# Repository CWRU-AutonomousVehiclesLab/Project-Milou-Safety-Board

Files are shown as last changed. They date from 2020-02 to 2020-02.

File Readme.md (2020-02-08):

# Project Milou Safety Board
This repo contains Project Milou's safety board design. The goal of this design is to have a standardized modular designed board that allow other competitor to improve their safety system.





## What is Project Milou?
Project Milou is Case Western Reserve University's second autonomous snowplow robot. The robot actively participate in the ION Autonomous Snowplow Challenge. Currently the latest revision of the robot is utilizing a Teensy 3.6, an ITX computer with a core i5 as its main control system.

## Logistics

**Latest revision is done at Febuary, 2020.**

The designer of this board can be traced back maybe 5 years, designed by folks working with Project Otto. This board re-layed out by Ziyi Huang as part of fullfilment for his senior project fall 2019. The board is modified by Frank (Chude Qian) to make it work on the robot. 

This project is maintained under CWRU Auontomous Vehicles Lab till 2021, and further maintained under CWRU Biologically Inspired Robotics (Biorobotics) Center. 

*Copyright belongs to CWRU Autonomous Vehicles lab, CWRU Biologically Inspired Robotics (Biorobotic) Center. Please use with acknowledgement.*

### Contact for questions
To contact email [Frank](mailto:cxq41@case.edu) if it is before 2021. If it is after 2021, email [Ian](mailto:ija2@case.edu) and [Dr. Merat](mailto:flm@case.edu). 

## How to use this?
To use the safety board design, you do not necessarily need to know about making PCBS. We recommend you to have some basic understanding of Egale the PCB software if you want to modify it. It should be fairly easy to use on a standardized ROS enabled robot.

### Pressumptions
The board assumes the following components: a 5V supply, a 12V supply, a standard RC Spread Specturum 2.4G remote reciever, a digital microcontroller that is capable of 5V or 3.3V digital input and output, a standard E-stop Button and a 12V relay.

### Materials
In order to use this PCB board, you will have to manufature it. We recommend [JLCPCB](https://jlcpcb.com/) which only cost about 10 USD for 5 boards. Unless you are mass manufacturing it, for sampling purposes, it should be good enough.

### Putting it together
In BOM folder, you will be able to find an excel sheet where it includes all of the materials you will need to put the board together. **NOTE: Do not use the value on the Eagle Schematics as they might by faulty. It is only used for manufacturing the PCB purpose.**

### 5V or 3.3V?
This board supports both 5V logic system and 3.3V logic system. If you need to have the logic output of the board to a 5V system, you should not solder R19 and R17 (aka a voltage divider to step down the 5V logic).

If your input voltage is normally 5V, I would recommend you use the Q4 component for Q5, instead of listed.

### Wiring it up!
Once you have completed all the steps above, you should be able to wire it up. To do so, start from left to right. The left side are all of the inputs.

**Supply**: The top of the supply terminal is +5V logic voltage, it is also used to power your Remote Reciever. A Ground is then followed. A 12V rail for driving the relay, and another ground.

**RCV-CH3**: For this 4 pin terminal, the top pin is your actual signal, and the middle one is 5V, and the bottom one is GND. Note that the last pin is not used, and additionally, the 5V pin can be disconnected if your RC reciever runs on a different voltage system. However, make sure that your GND is connected so that the system runs on the same reference.

**TEENSYIN** For this terminal, the top two are responsible for tracking the microcontroller output. This is designed allowing the microcontroller to throw an Estop exception and allowing the robot to be safely disabled from software. If your design do not have this feature, simply follow the 5V logic guideline and apply 5V directly on to the terminal. The bottom two are responsible for the Red ESTOP button. Simply wire the button to those two leads.

**TEENSYOUT** This is 4pin terminal on the right. This is all the output terminals. The top 2 terminals are wired directly to a relay to further drive a contactor for the robot. These two pin will run on 12V so make sure not to get it onto your microcontroller. The bottom two are signal for the microcontroller, allowing it to read the state of the ESTOP board. As always, top is signal, and bottom is GND. 

The board is designed to provide you ground wherever you might needed. For best practice you can also use twisted cable for delivering signal and reduce circuit noise interference.

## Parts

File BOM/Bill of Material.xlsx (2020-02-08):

Part | Value | Device | Package | Description | Multi Voltage OP Note
RCV_CH3 | 1X4-CLEANBIG | 1X4-CLEANBIG | 1X04-CLEANBIG | 4-pin connector
SUPPLY | 1X4-CLEANBIG | 1X4-CLEANBIG | 1X04-CLEANBIG | 4-pin connector
TEENSYIN | 1X4-CLEANBIG | 1X4-CLEANBIG | 1X04-CLEANBIG | 4-pin connector
TEENSYOUT | 1X4-CLEANBIG | 1X4-CLEANBIG | 1X04-CLEANBIG | 4-pin connector
C3 | .1uF | C10/4 | C10B4 | CAPACITOR
C4 | .1uF | C10/4 | C10B4 | CAPACITOR
C1 | .01uF | C5/2.5 | C5B2.5 | CAPACITOR
C2 | .01uF | C5/2.5 | C5B2.5 | CAPACITOR
C5 | .01uF | C5/2.5 | C5B2.5 | CAPACITOR
C6 | .01uF | C5/2.5 | C5B2.5 | CAPACITOR
C7 | .01uF | C5/2.5 | C5B2.5 | CAPACITOR
C8 | .01uF | C5/2.5 | C5B2.5 | CAPACITOR
U3 | SN74HC08N | SN74HC08N | DIP254P762X508-14 | QUADRUPLE 2-INPUT POSITIVE-NOR GATES
U4 | SN74HC74N | SN74HC74N | DIP254P762X508-14 | DUAL D-TYPE POSITIVE-EDGE-TRIGGERED FLIP-FLOPS
U1 | NE555 | NE555 | DIP794W45P254L1060H508Q8 | 555 timer
U2 | NE555 | NE555 | DIP794W45P254L1060H508Q8 | 555 timer
D3 | 1N4446 | 1N4446 | DO35-10 | DIODE
D1 | 1N4004 | 1N4004 | DO41-10 | DIODE
R1 | 10K | RHPS58 | HPS58 | Power Resitor
R10 | 10K | RHPS58 | HPS58 | Power Resitor
R11 | 10K | RHPS58 | HPS58 | Power Resitor
R12 | 1K | RHPS58 | HPS58 | Power Resitor
R13 | 1K | RHPS58 | HPS58 | Power Resitor
R14 | 1K | RHPS58 | HPS58 | Power Resitor
R15 | 33K | RHPS58 | HPS58 | Power Resitor
R16 | 33K | RHPS58 | HPS58 | Power Resitor
R17 | 33k | RHPS58 | HPS58 | Power Resitor | Optional, not needed for 5v output
R18 | 5.6K | RHPS58 | HPS58 | Power Resitor
R19 | 56k | RHPS58 | HPS58 | Power Resitor | Optional, not needed for 5v output
R2 | 10K | RHPS58 | HPS58 | Power Resitor
R3 | 10K | RHPS58 | HPS58 | Power Resitor
R4 | 10K | RHPS58 | HPS58 | Power Resitor
R5 | 10K | RHPS58 | HPS58 | Power Resitor
R6 | 10K | RHPS58 | HPS58 | Power Resitor
R7 | 15K | RHPS58 | HPS58 | Power Resitor
R8 | 200K | RHPS58 | HPS58 | Power Resitor
R9 | 10K | RHPS58 | HPS58 | Power Resitor
LED1 | RED | LED3MM | LED3MM | LED
Q4 | IRF530 | MOSFET-NGDS_TO220V | TO220V | N-Channel Mosfet
Q5 | IRLZ44N | MOSFET-NGDS_TO220V | TO220V | N-Channel Mosfet | Exchangable for 5V operation
Q3 | 2N4403 | 2N4403 | TO92-EBC-OVAL | PNP TRANSISTOR
T1 | 2N4401 | 2N4401 | TO92-EBC-OVAL | NPN TRANSISTOR
T2 | 2N4401 | 2N4401 | TO92-EBC-OVAL | NPN TRANSISTOR
T3 | 2N4401 | 2N4401 | TO92-EBC-OVAL | NPN TRANSISTOR
T4 | 2N4401 | 2N4401 | TO92-EBC-OVAL | NPN TRANSISTOR

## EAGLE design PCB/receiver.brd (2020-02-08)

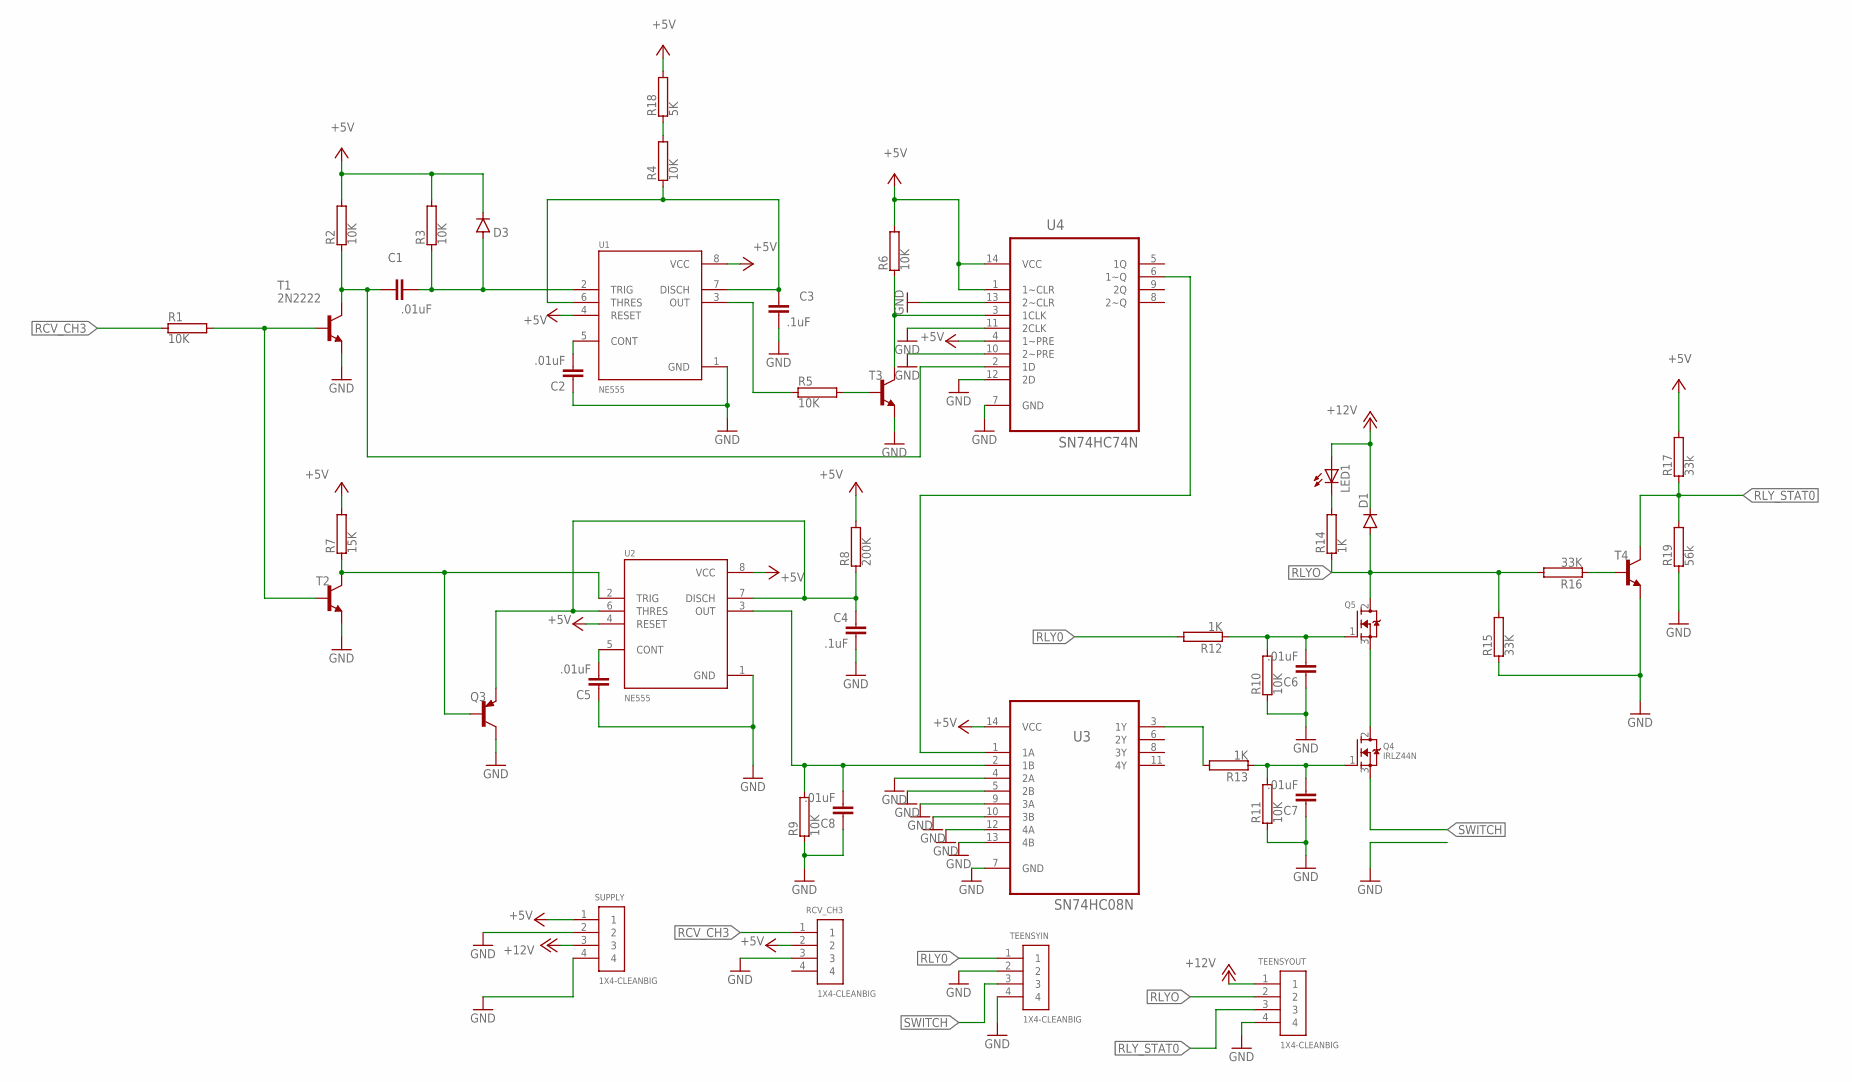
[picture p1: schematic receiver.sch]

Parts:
C1, C2, C5, C6, C7, C8: .01uF; C5B2.5
C3, C4: .1uF; C10B4
D1: 1N4004; DO41-10
D3: 1N4446; DO35-10
LED1: LED3MM
Q3: 2N2907; TO92-EBC-OVAL
Q4: IRLZ44N; TO220V
Q5: MOSFET-NGDS_TO220V; TO220V
R1, R2, R3, R4, R5, R6, R9, R10, R11: 10K; HPS58
R7: 15K; HPS58
R8: 200K; HPS58
R12, R13, R14: 1K; HPS58
R15, R16: 33K; HPS58
R17: 33k; HPS58
R18: 5K; HPS58
R19: 56k; HPS58
RCV_CH3: 1X4-CLEANBIG; 1X04-CLEANBIG
SUPPLY: 1X4-CLEANBIG; 1X04-CLEANBIG
T1, T2, T3, T4: 2N2222; TO92-EBC-OVAL
TEENSYIN: 1X4-CLEANBIG; 1X04-CLEANBIG
TEENSYOUT: 1X4-CLEANBIG; 1X04-CLEANBIG
U1, U2: NE555; DIP794W45P254L1060H508Q8
U3: SN74HC08N; DIP254P762X508-14
U4: SN74HC74N; DIP254P762X508-14

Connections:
+5V: D3.C, R2.2, R3.2, R6.2, R7.2, R8.2, R17.2, R18.2, RCV_CH3.2, SUPPLY.1, U1.4 (RESET), U1.8 (VCC), U2.4 (RESET), U2.8 (VCC), U3.14 (VCC), U4.1 (1~CLR), U4.4 (1~PRE), U4.14 (VCC)
+12V: D1.C, LED1.A, SUPPLY.3, TEENSYOUT.1
GND: C2.1, C3.2, C4.2, C5.1, C6.1, C7.1, C8.1, Q3.C, R9.1, R10.1, R11.1, R15.1, R19.1, RCV_CH3.3, SUPPLY.2, SUPPLY.4, T1.E, T2.E, T3.E, T4.E, TEENSYIN.2, TEENSYIN.4, TEENSYOUT.4, U1.1 (GND), U2.1 (GND), U3.4 (2A), U3.5 (2B), U3.7 (GND), U3.9 (3A), U3.10 (3B), U3.12 (4A), U3.13 (4B), U4.7 (GND), U4.10 (2~PRE), U4.11 (2CLK), U4.12 (2D), U4.13 (2~CLR)
unnamed: R1.2, T1.B, T2.B
unnamed: C1.2, R2.1, T1.C, U4.2 (1D)
unnamed: C1.1, D3.A, R3.1, U1.2 (TRIG)
unnamed: C2.2, U1.5 (CONT)
unnamed: C3.1, R4.1, U1.6 (THRES), U1.7 (DISCH)
unnamed: R5.1, U1.3 (OUT)
unnamed: R5.2, T3.B
unnamed: R6.1, T3.C, U4.3 (1CLK)
unnamed: Q3.B, R7.1, T2.C, U2.2 (TRIG)
unnamed: C4.1, Q3.E, R8.1, U2.6 (THRES), U2.7 (DISCH)
unnamed: C6.2, Q5.1 (G), R10.2, R12.1
unnamed: C8.2, R9.2, U2.3 (OUT), U3.2 (1B)
unnamed: C5.2, U2.5 (CONT)
unnamed: U3.1 (1A), U4.6 (1~Q)
unnamed: R4.2, R18.1
unnamed: C7.2, Q4.1 (G), R11.2, R13.1
unnamed: R13.2, U3.3 (1Y)
unnamed: LED1.K (C), R14.2
unnamed: Q4.2 (D), Q5.3 (S)
unnamed: R16.1, T4.B
RCV_CH3: R1.1, RCV_CH3.1
RLY0: R12.2, TEENSYIN.1
RLYO: D1.A, Q5.2 (D), R14.1, R15.2, R16.2, TEENSYOUT.2
RLY_STAT0: R17.1, R19.2, T4.C, TEENSYOUT.3
SWITCH: Q4.3 (S), TEENSYIN.3

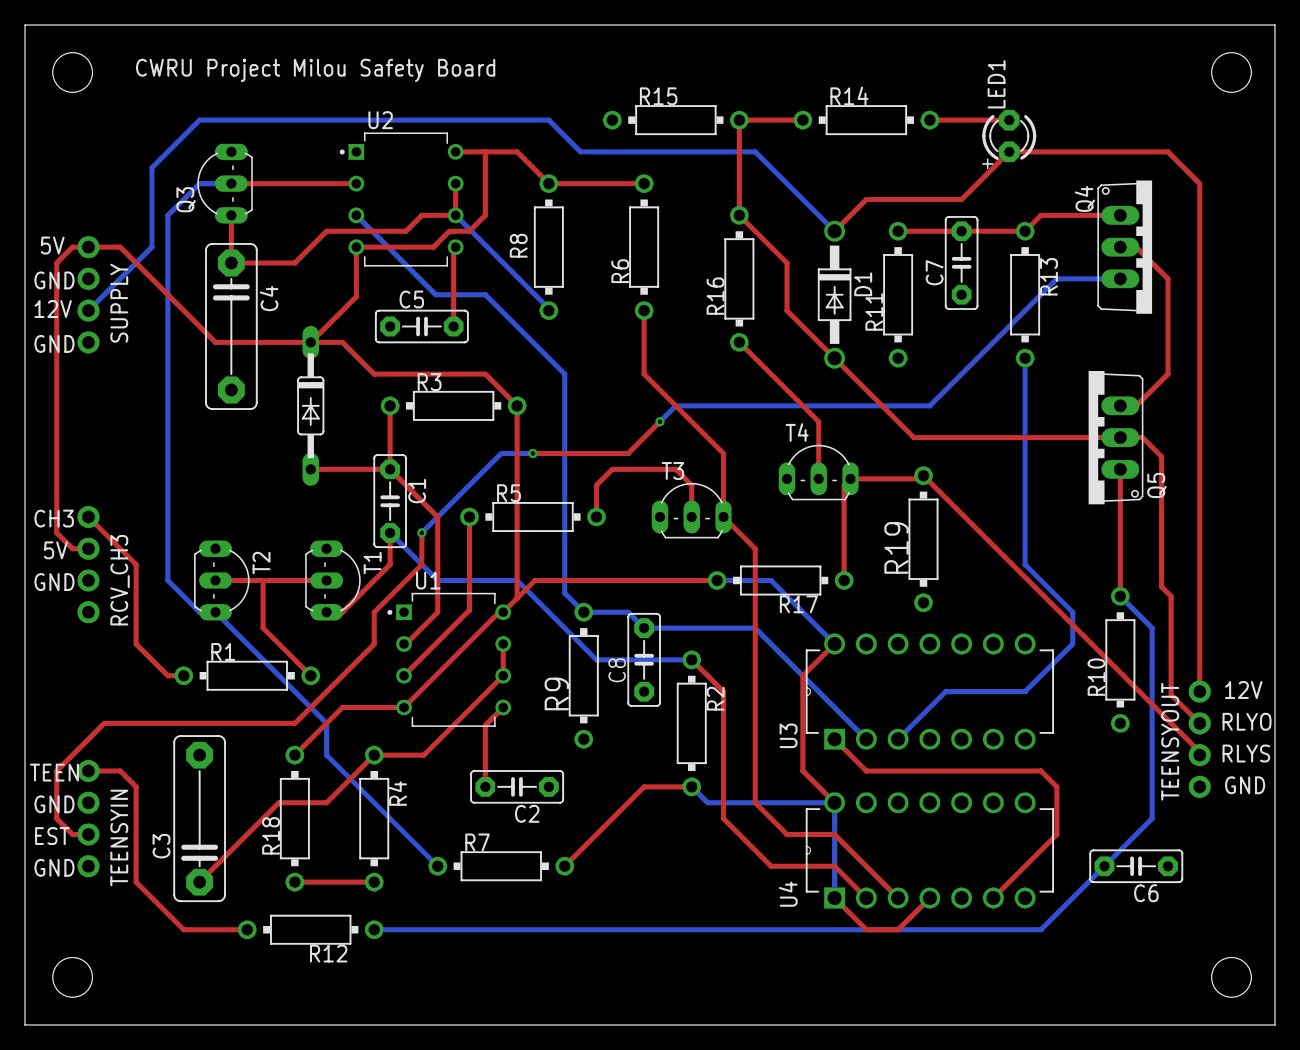
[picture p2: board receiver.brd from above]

Board: 2 copper layers, 100.0 x 80.0 mm, 45 parts (0 on the bottom side), 28 nets.

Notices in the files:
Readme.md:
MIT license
